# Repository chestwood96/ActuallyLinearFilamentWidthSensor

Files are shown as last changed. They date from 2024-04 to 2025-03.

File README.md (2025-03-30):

# ALFws (ActuallyLinearFilamentWidthSensor)
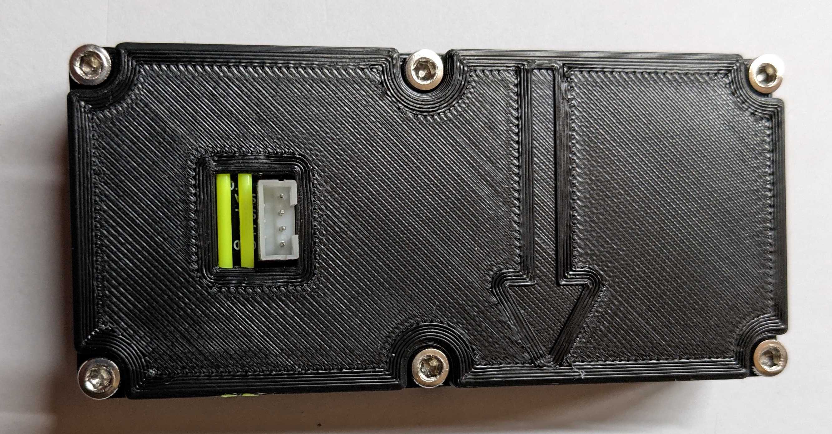
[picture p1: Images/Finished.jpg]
Finished sensor


## Features
### Sensor
- Very good linearity over 1mm (centred on ~1.75)
- Good linearity over 2-3mm (3mm filament is theoretically compatable, but remains untested)
- No thermal drift on the sensor
- Low drag
### Software
- Filament width compensation (of course)
- Logging filament diameter
- Undersize runout
- Oversize runout (so really oversized filament doesn't get stuck in the heatbreak)
- Delayed runout

## Why would you want that?
I mainly started this project ages ago because my local filament manufacturer doesn't know what QC is and happily ships filament with more than +/- 0.25mm tolerances. This isn't my first attempt at a filament width sensor but it is by far my best. With this I can print massively undersized or oversized or perfectly sized filament without ever having to touch my extrusion multiplier.

## BOM
### Electronics
- 1x [Sensor PCB](PCB/README.md)
- 1x JST PH 4pin female cable
### Mechanical
- 2x 6804 ball bearing
- 2x 6x3mm OR 1x 6x6mm magnet (if you can, get SmCO ones, they have less thermal drift)
- 2x 5x15 coil spring, 0.6mm wire diameter OR 8x 6x3mm neodymium magnets, the cheap kind
- 8x m3x8 screws
### Tools
- Fine-ish sanding pad/sandpaper
- Pliers
- Sidecutters
- Hammer or some other heavy object to hit stuff with
- 1.5mm and 2mm drill bit or other cylindrical metal objects of known size in that range for calibration

## Printing
Unless you want to constantly recalibrate this thing you need to print it in ABS or some other option that doesn't creep (definitely not PLA or Nylon), also avoid fiber filled filaments. The files are designed to print in the orientation they come in and do not require supports.

For MainBody **IRONING IS REQUIRED** since it is pretty much impossible to sand the inside sliding surface well enough, for the rest except the lid it is just highly recommended.

Except for MainBody the parts **need to be printed on a smooth buildplate**.

Use at least 3 perimeters and 5 top and bottom layers.

# Build
This is kind of a precision instrument and the quality of the final result heavily depends on how well it was assembled. Unfortunately this involves sanding.
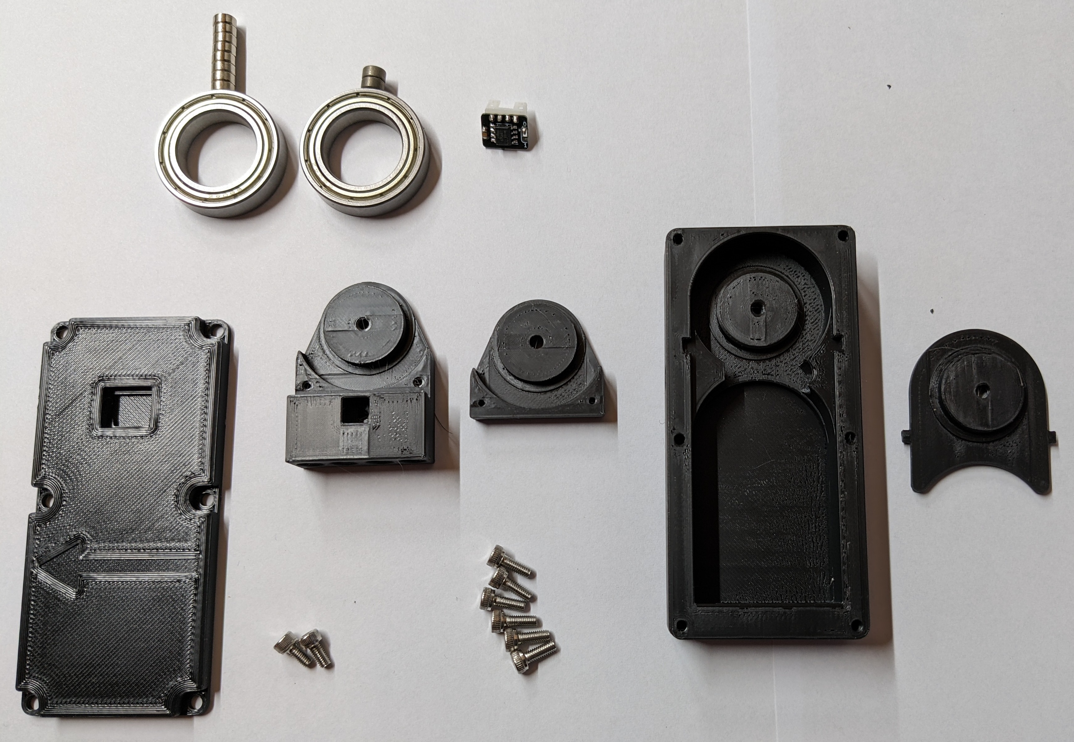
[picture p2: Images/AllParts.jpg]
All the parts layed out

Pretend the two m3x6 screws on this picture are also m3x8

## Cleaning up MainBody
Make sure the walls of the sliding surface on the bottom and the sides are smooth and have nothing sticking out. In most cases this should be fine off the printer but in this one there was a little defect in the walls. Also make sure the top surface for the lid is smooth and flat.
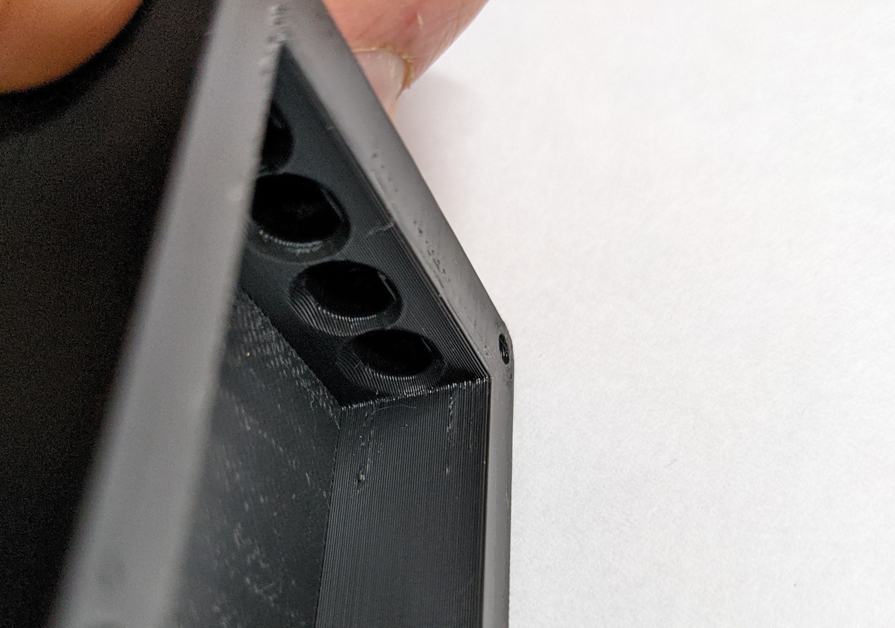
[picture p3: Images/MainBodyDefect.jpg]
Defect in MainBody

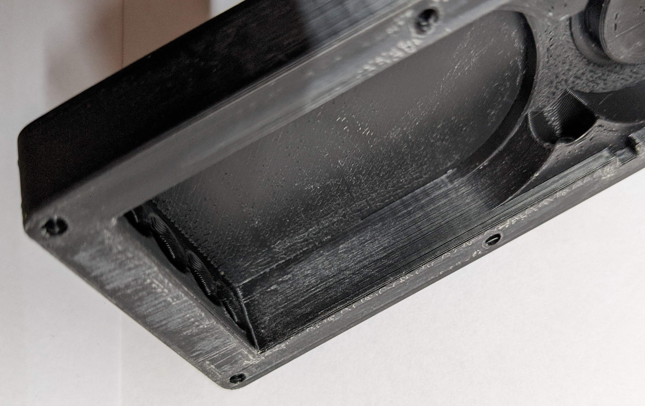
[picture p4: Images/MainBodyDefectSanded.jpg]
Defect in MainBody sanded

## Assembling the plunger
Place the bearing on MainPlunger and place BearingTop on top of that.
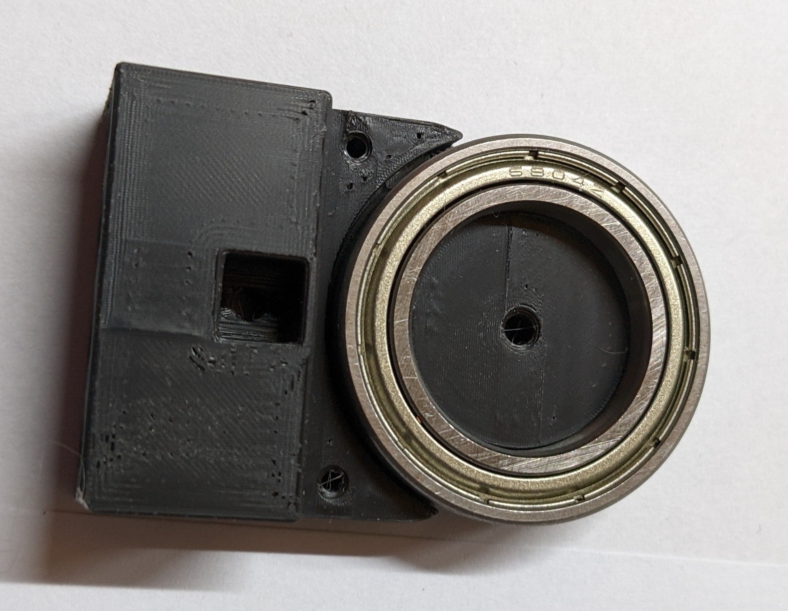
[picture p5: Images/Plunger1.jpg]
MainPlunger

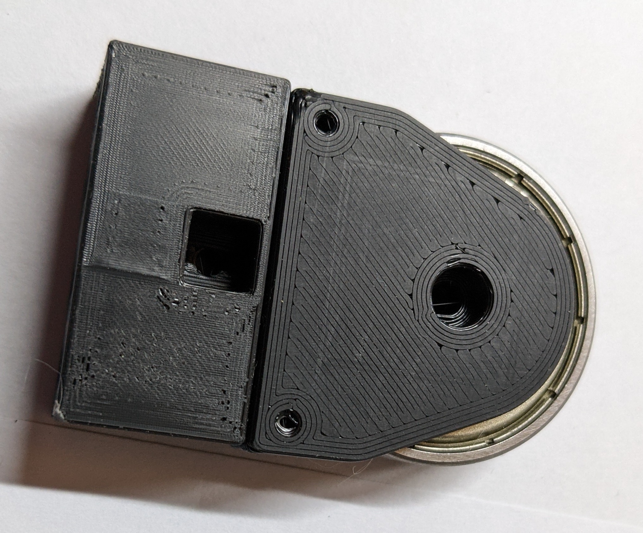
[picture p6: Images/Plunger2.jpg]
MainPlunger with BearingTop

Take a piece of the filament you printed with, sharpen the end, then push it through the pin hole. You may need to drill out the holes in BearingTop if the filament doesn't fit. Push them in most of the way, cut the filament a couple mm from the top, and hammer it in the rest of the way. Once it is all the way in snip it off as flush as you can.
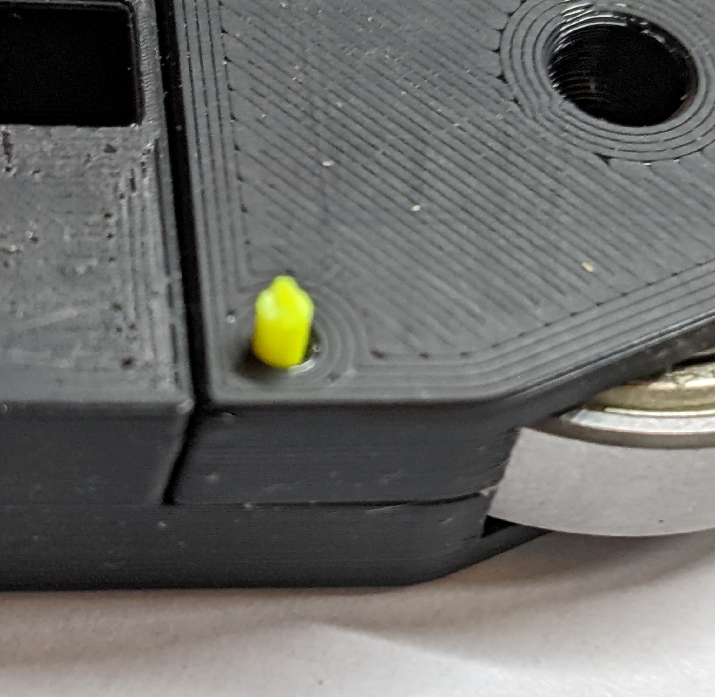
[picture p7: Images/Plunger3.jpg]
Plunger with pin in one side

Screw the bearing down using an m3x8 screw.
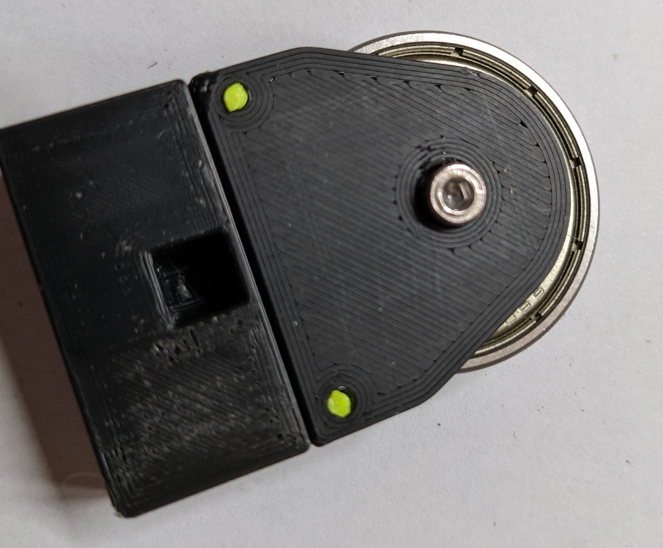
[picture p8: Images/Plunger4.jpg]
Plunger with pin in one side

Place your magnets (the nice ones if you got them) in the slot and gently (SmCO magnets are quite fragile and chip easily) press them all the way down, they should be a little bit below the surface of the part. They should be held in place pretty well. **If they don't sit in there snugly, glue them down using epoxy or something**, we don't wan't wobbly magnets.
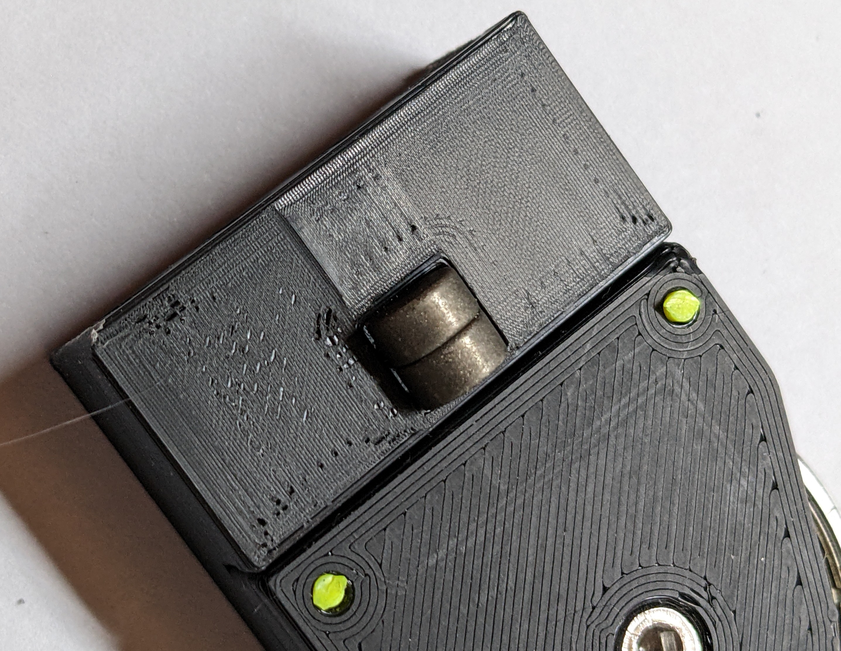
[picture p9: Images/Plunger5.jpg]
Magnet in slot

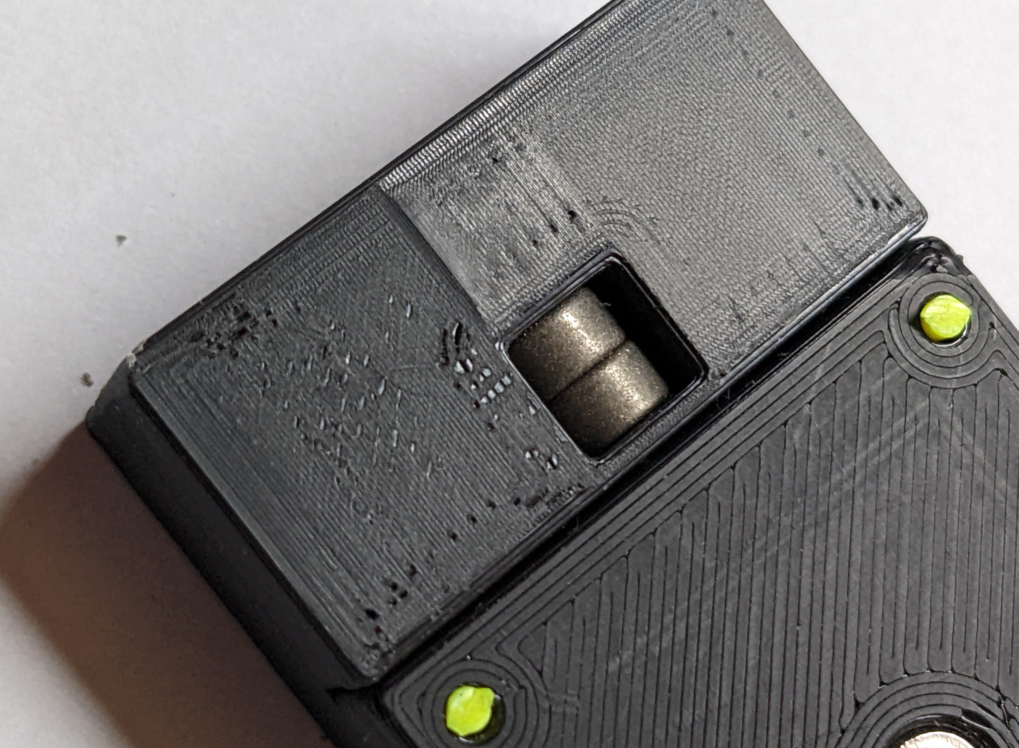
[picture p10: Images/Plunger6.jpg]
Magnet in slot all the way down


## Fitting the plunger
**Only sand with the sandpaper below the part** and avoid getting dust into the bearing, or it will seize and become crunchy. It is recommended to fix the sandpaper to a flat surface and move the part across the sandpaper. This avoids inadvertently making the part unlevel.

Sand the sides of the plunger until it slides smoothly. You don't want to sand too much otherwise you'll get side to side play.
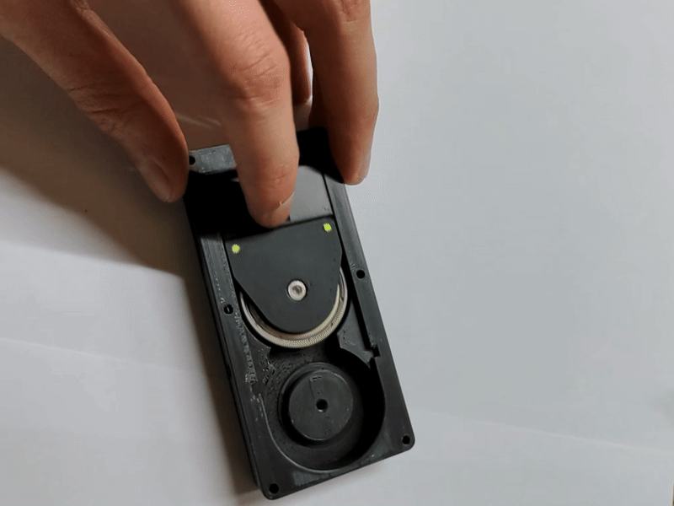
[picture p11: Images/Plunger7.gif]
Plunger sliding smoothly


*If you are using coil springs skip this step*

Push 2 magnets into each of the outer holes on the plunger, both facing in the same direction. The inner holes remain unused (could be used for more magnets if for some reason more spring force is required)
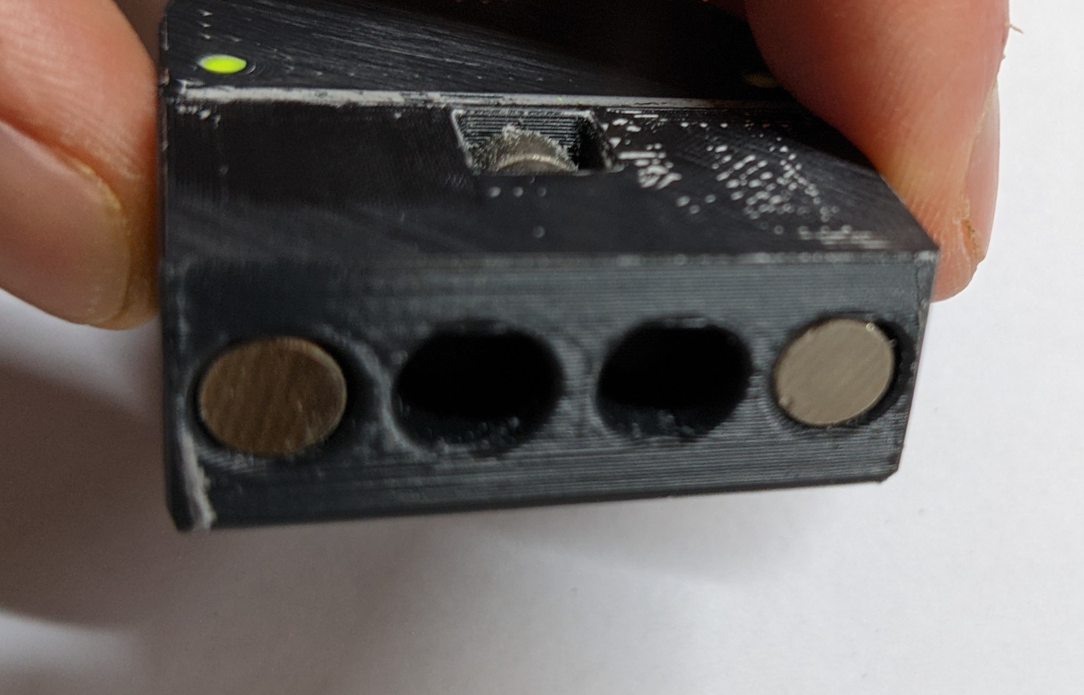
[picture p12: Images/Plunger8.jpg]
Magnets in plunger

Sand down the top of the plunger (the bottom should already be smooth) until you can freely shake it around with the lid closed. Start by just holding the lid closed by hand (only grip at the corners) and then when that works screw in the 2 middle screws and check again. You want to remove as little as possible so you get smooth motion and not a lot of play.
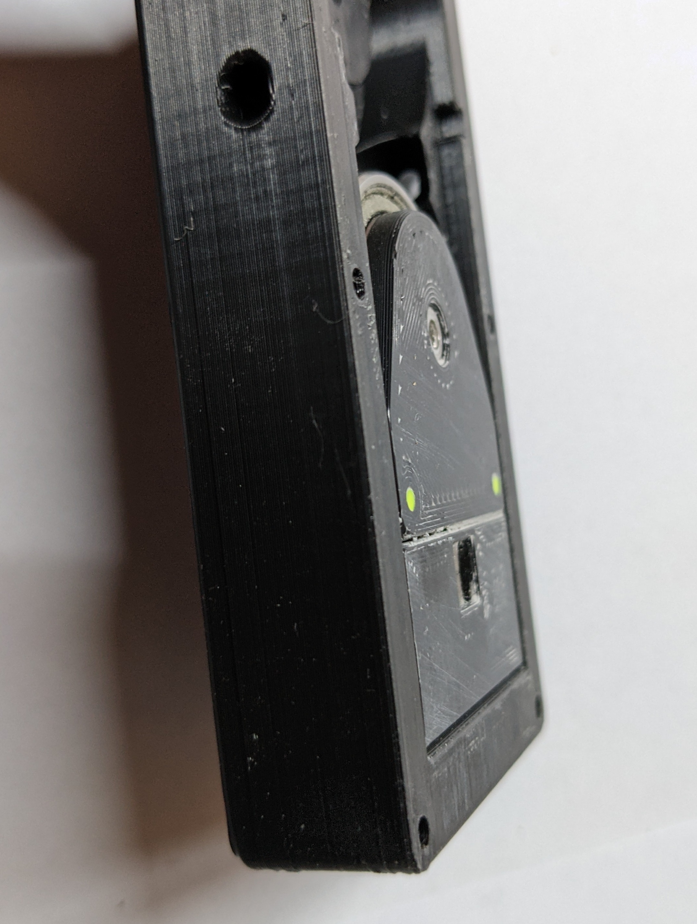
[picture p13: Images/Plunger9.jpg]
Sanded Plunger

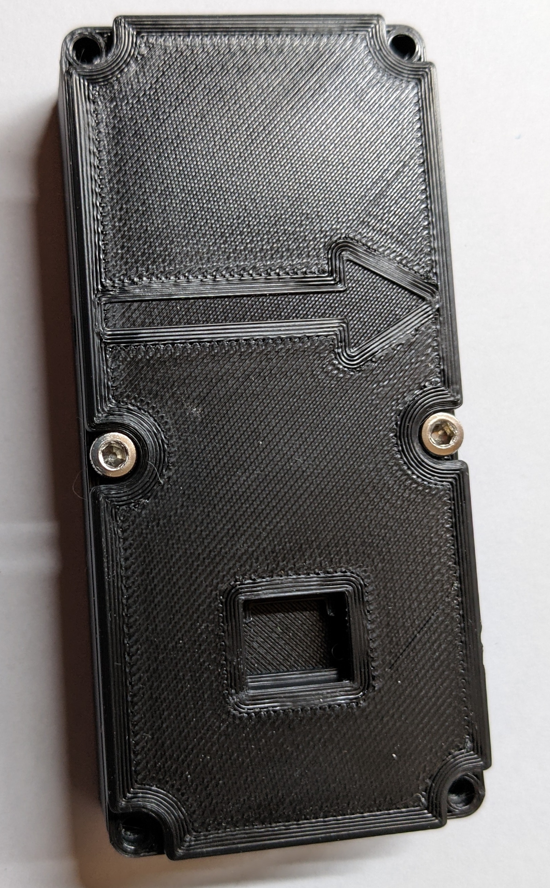
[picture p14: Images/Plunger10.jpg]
Sensor closed for testing


## Putting it all together
*If you are using coil springs skip this step*

Put the other 2 stacks of magnets into the holes as shown. The plunger should be attracted to the back of the sensor body like in the second picture. The magnets should now work as springs.
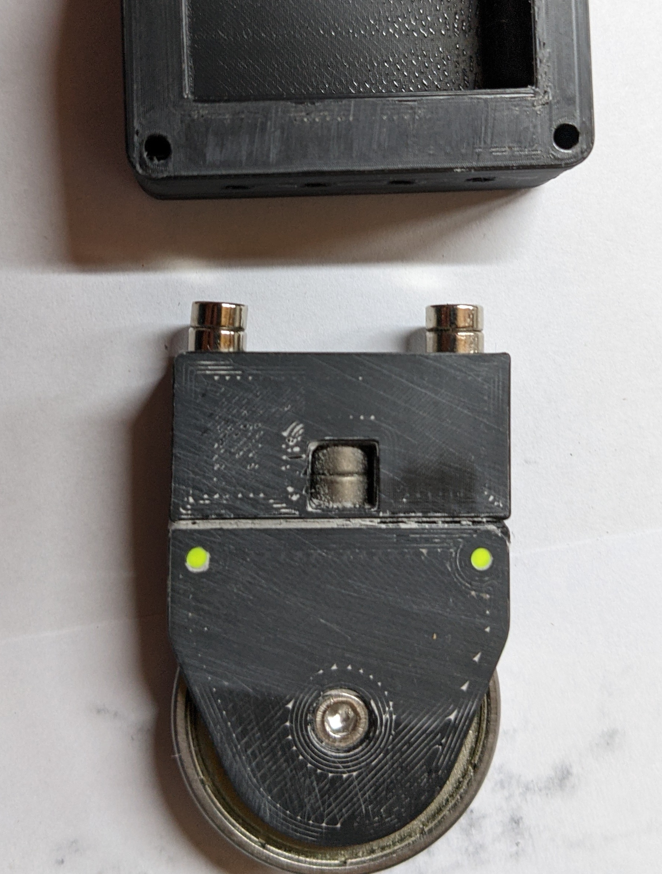
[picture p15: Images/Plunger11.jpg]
Magnets on the plunger

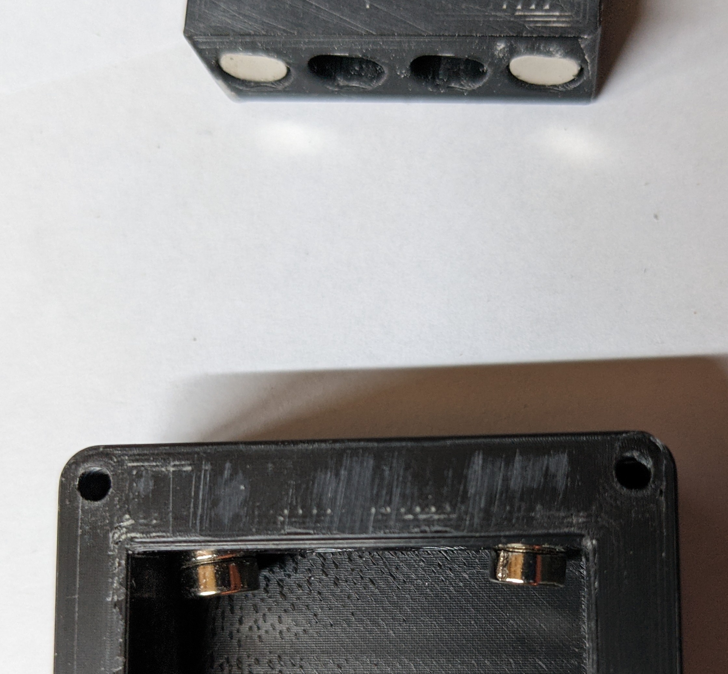
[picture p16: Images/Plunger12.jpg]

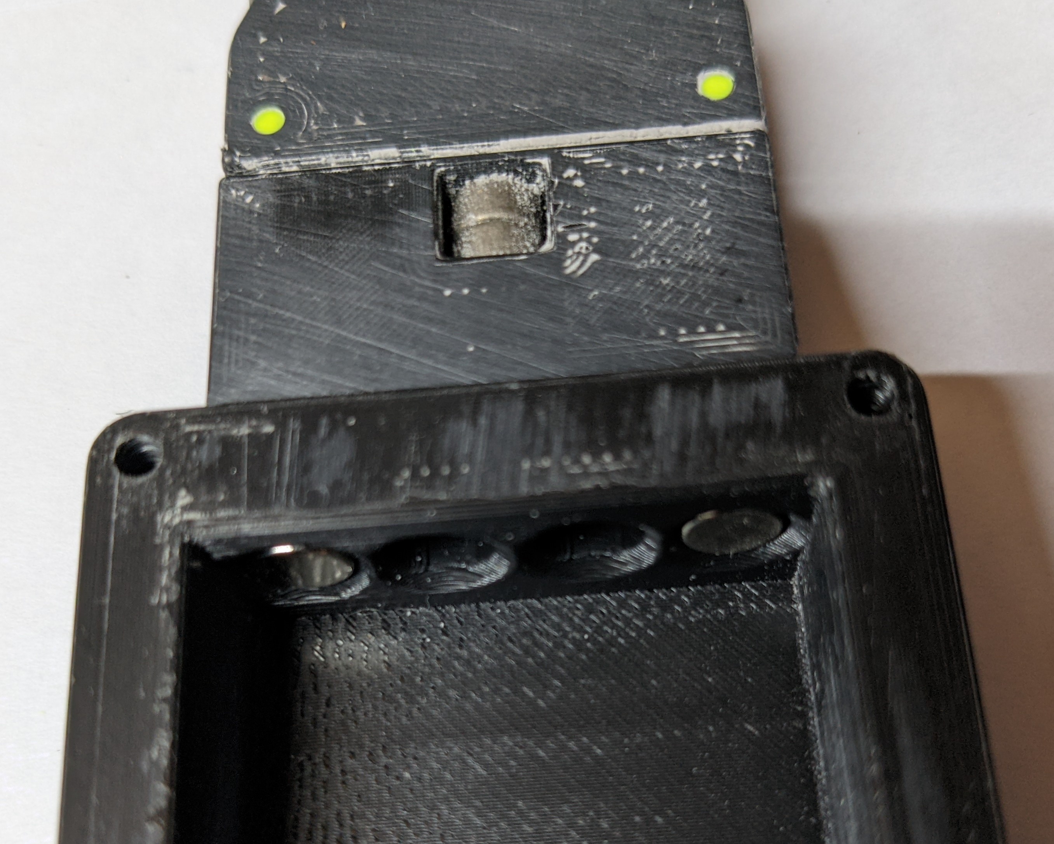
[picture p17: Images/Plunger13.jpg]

Demonstration of the magnet spring
Put the second bearing into MainBody, put BodyBearingHolder on top of it and screw it down. The bearing holder should not stick out the top, if it does sand it down.
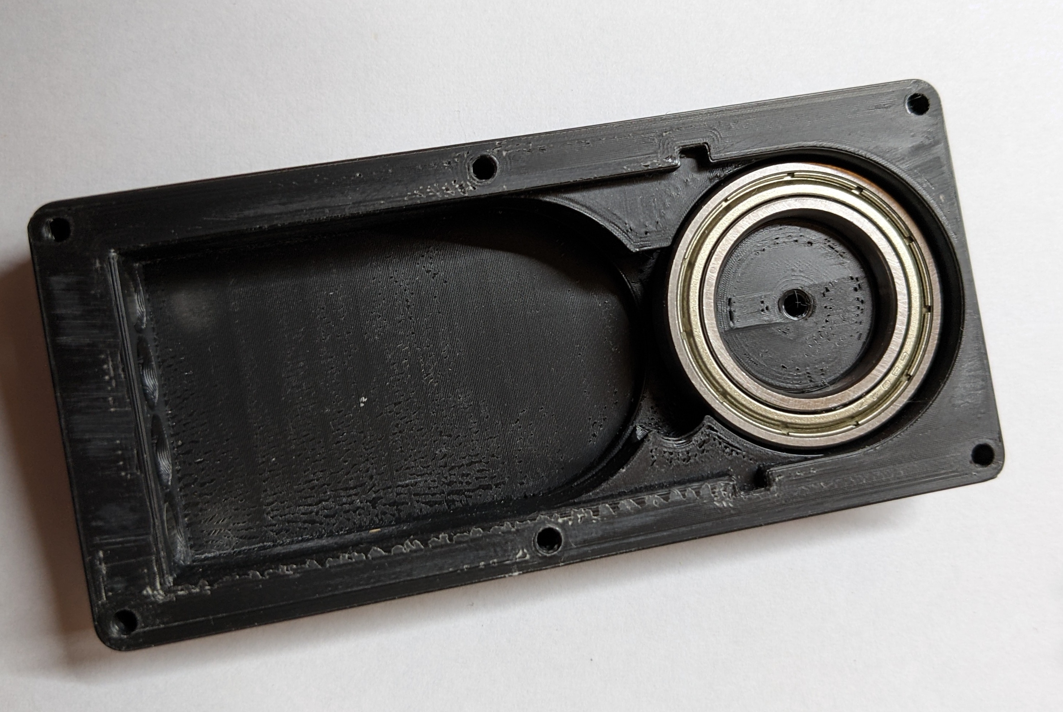
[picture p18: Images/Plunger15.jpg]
Bearing in body

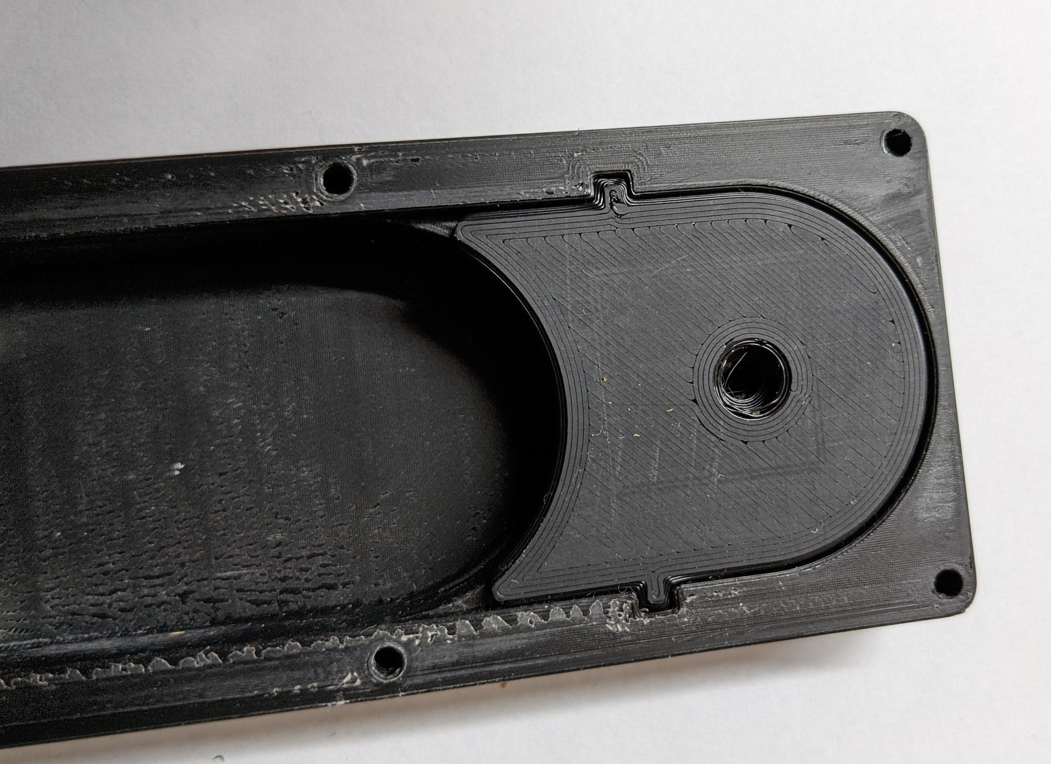
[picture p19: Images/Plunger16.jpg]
Bearing holder in body

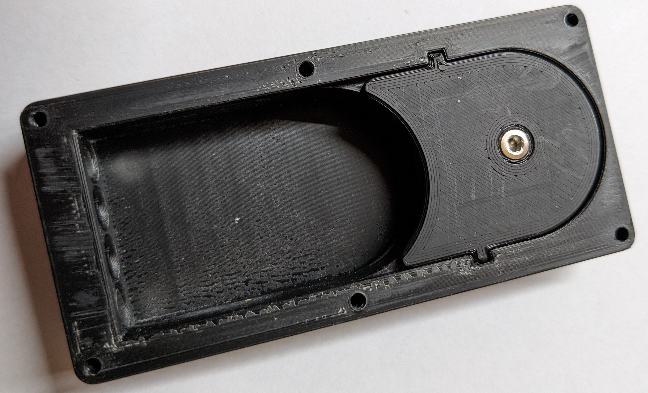
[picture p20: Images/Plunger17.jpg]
Bearing holder screwed down


*If you are using coil springs put the springs into the outer holes when putting in the plunger*

Place the plunger into the body. It's normal that the bearings don't completely touch when closed but they should get within less than 1mm.
Bearing holder screwed down

## Putting the sensor in the lid
**While the sensor is still free, note what jumper value is set because you won't be able to see it later, and if none is set fix that**

Gently push the sensor board into the hole in the lid as shown.
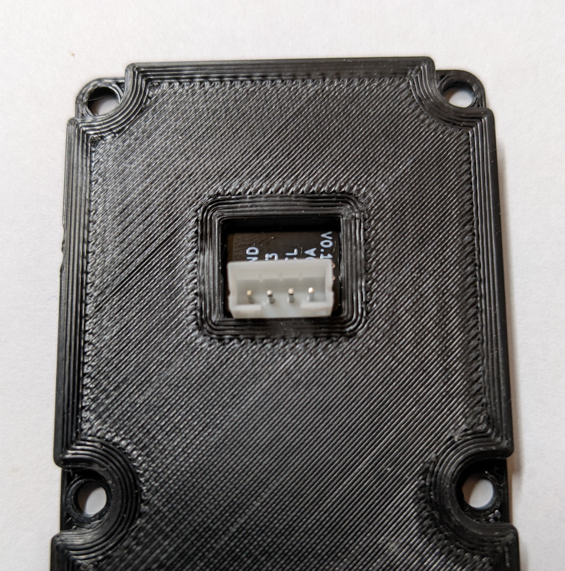
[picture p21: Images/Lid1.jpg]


Push a sharpened piece of ABS filament into the hole on the side of the lid, over the sensor and into the hole on the other side. Once you reach the entrance of the inner hole, cut the filament about 2mm from the side and hammer it the rest of the way in, it should be flush otherwise cut the rest off. Then repeat for the second hole.

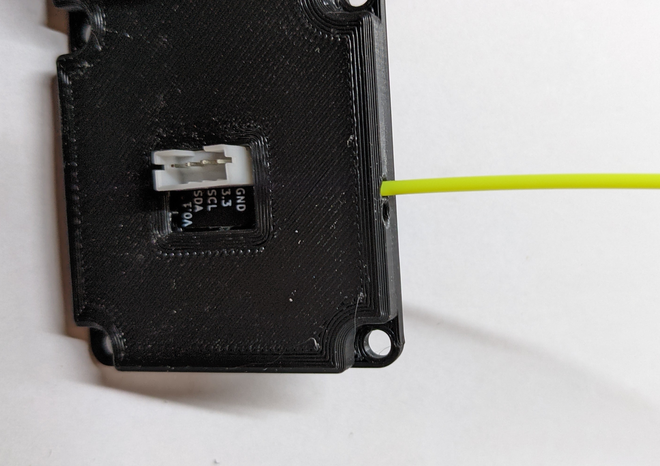
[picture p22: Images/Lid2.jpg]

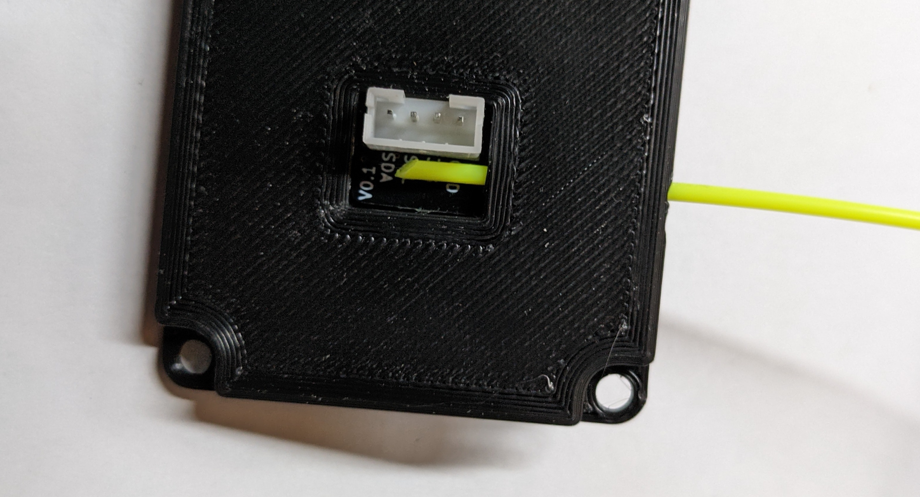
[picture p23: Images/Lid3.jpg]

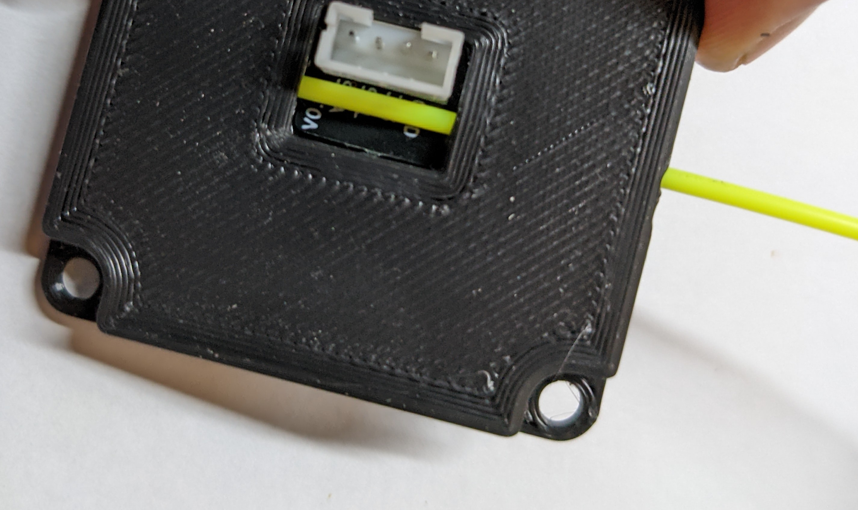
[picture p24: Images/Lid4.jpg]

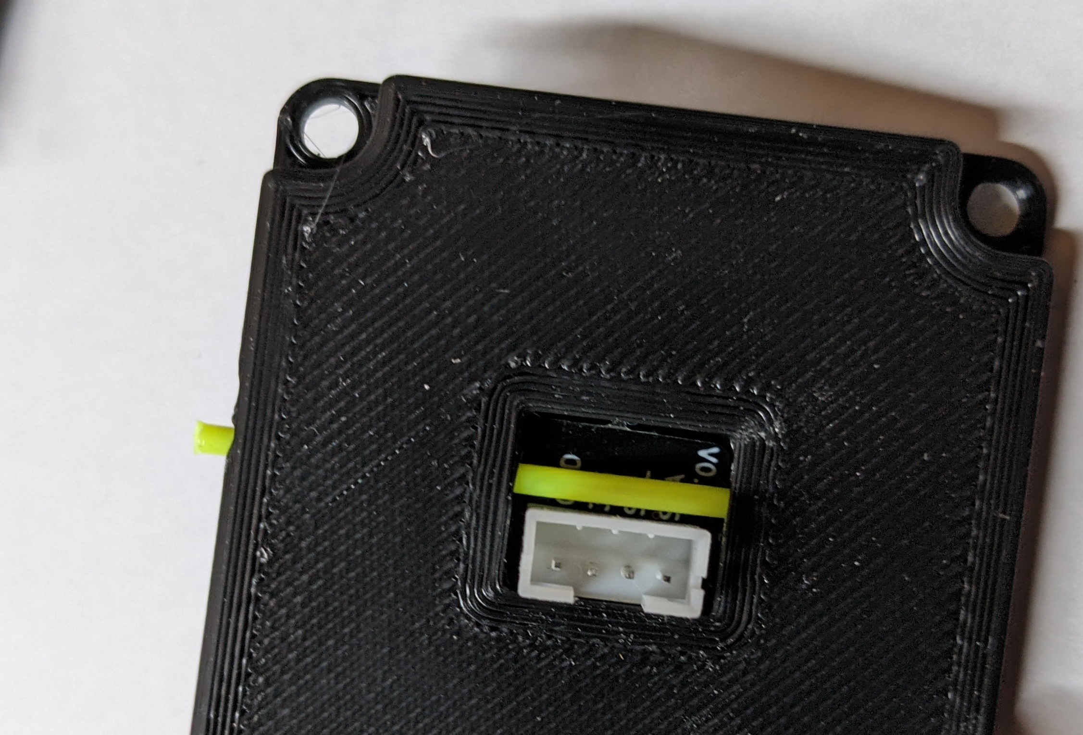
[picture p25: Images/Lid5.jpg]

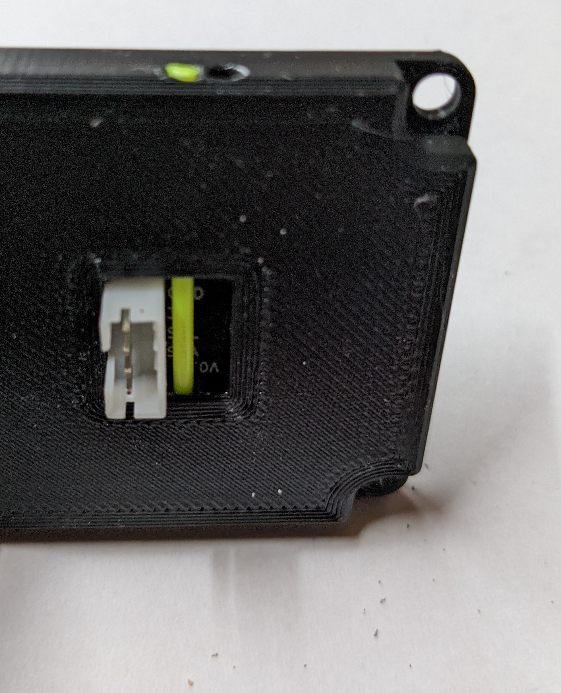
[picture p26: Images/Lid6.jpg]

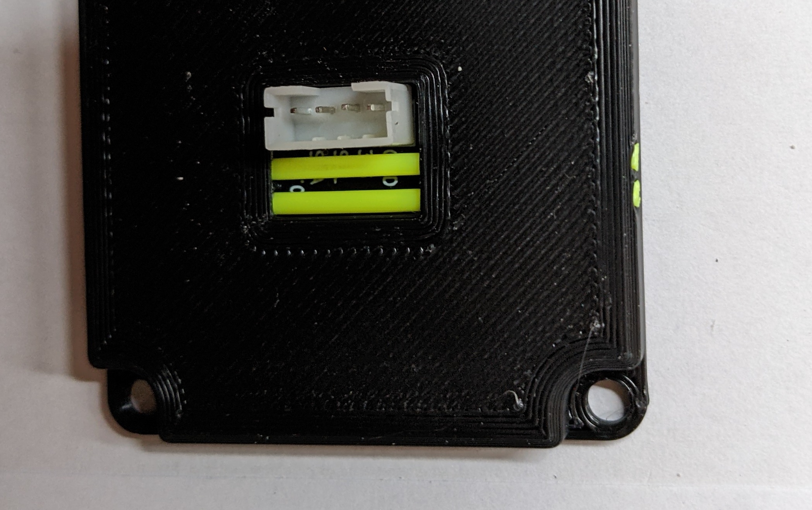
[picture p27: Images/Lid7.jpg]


## Putting on the lid
Make sure the sensor part is over the magnet in the plunger and close the lid using 6 m3x8 screws.
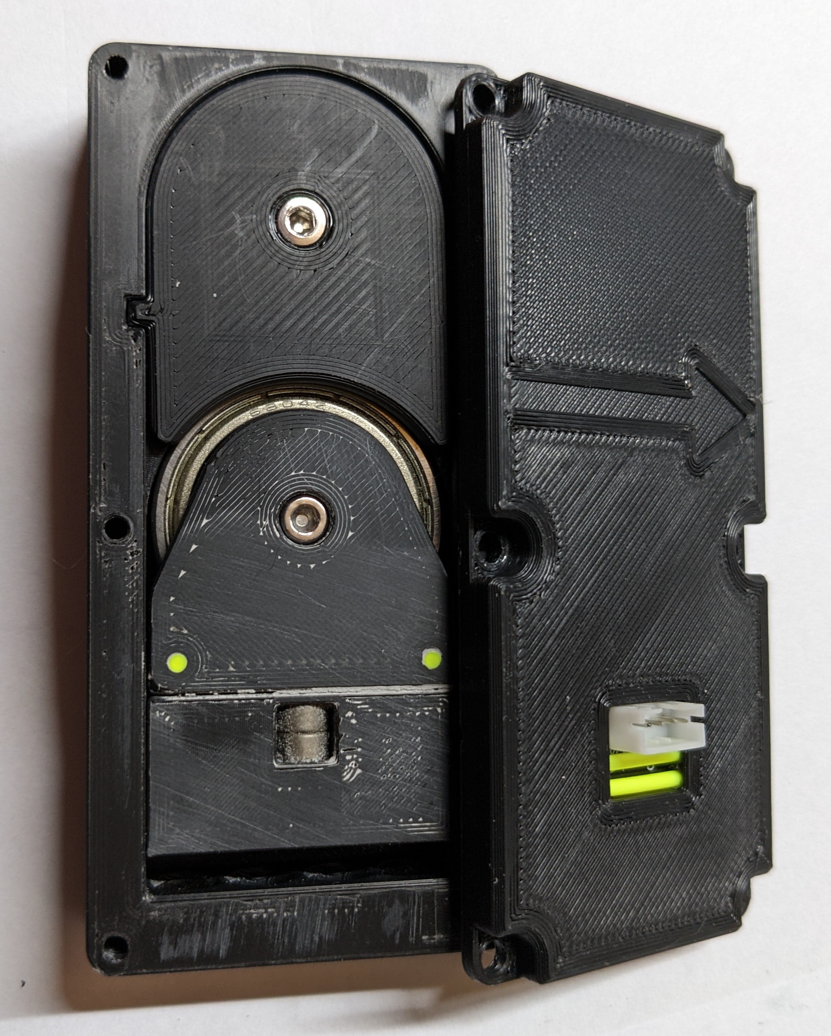
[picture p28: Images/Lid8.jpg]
Lid orientation

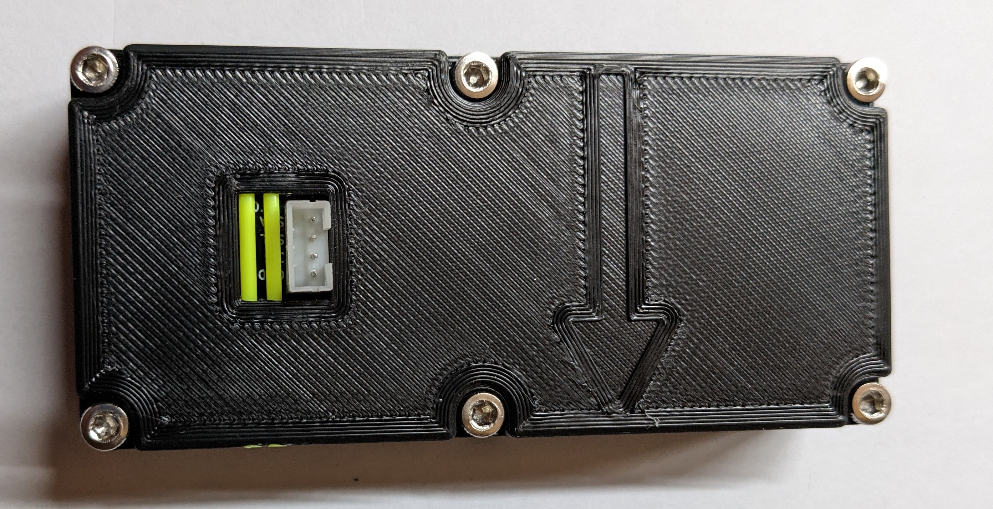
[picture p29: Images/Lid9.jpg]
Done


**Congratulation the sensor is built** 

Stick some filament in it, check if the bearings are running smoothy and the plunger closes up correctly once you pull it back out.

# Installation

## Wiring
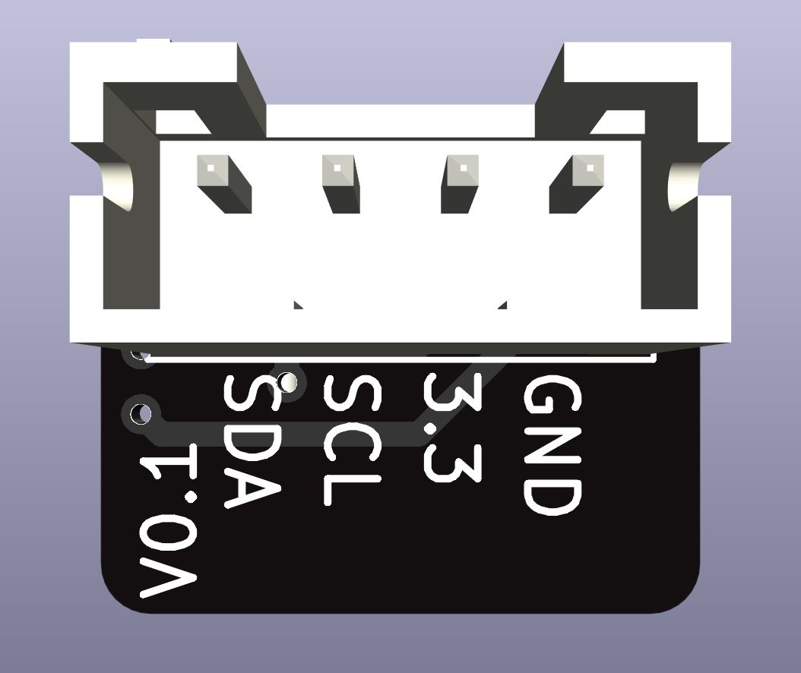
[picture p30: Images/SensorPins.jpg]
Sensor pins

**If you are somehow still on a platform with 5V IO pins you are going to need a level shifter for SDA and SCL. Examples include ATMEL based boards like ramps and the old creality boards. If in doubt measure the voltage on the SDA pin before connecting.**

Find an available I2C port on yur mainboard and connect the sensor to it. While you can theoretically use any pins with software I2C, I recommend using HW I2C since the sensor produces quite a bit of I2C traffic which would take up quite a lot of the MCUs computing power.

For example I use the I2C port on PB8 and PB9 on the octopus pro.
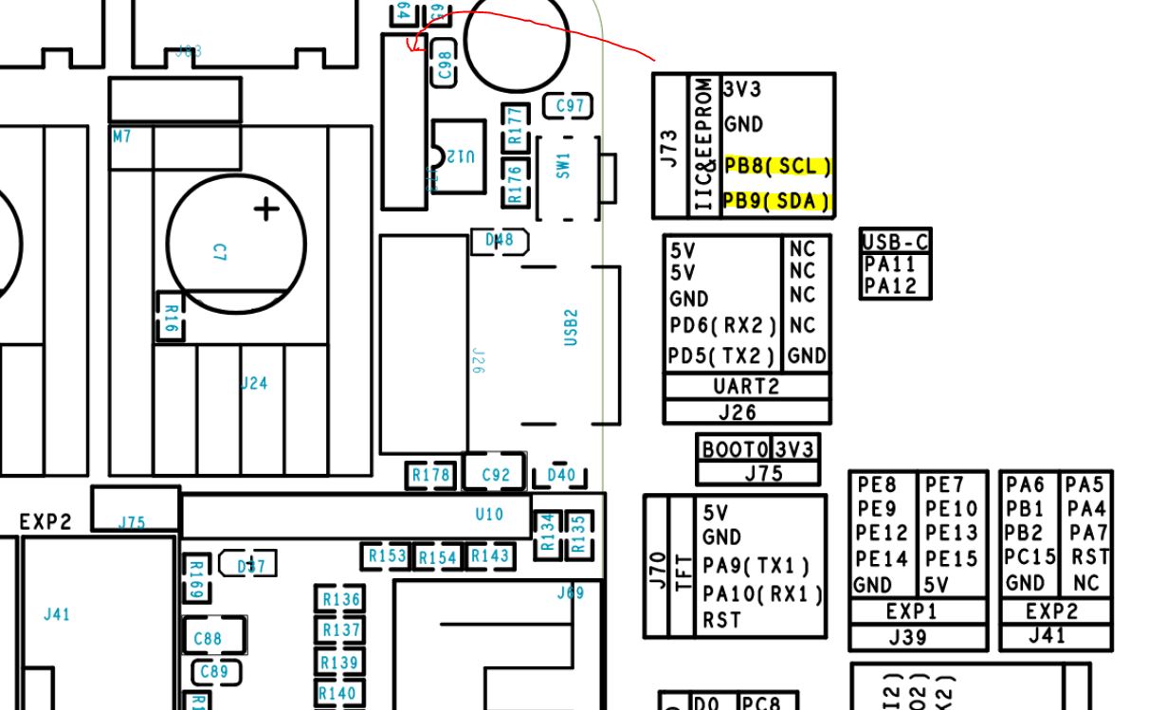
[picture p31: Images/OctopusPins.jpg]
Octopus pro i2c


Alternatively you could use a separate microcontroller like a Pi Pico, STM32 bluepill or anything else supported by Klipper.

Simply connect the pins on the sensor to the corresponding ones on your board (GND to GND, 3.3V to 3.3V, SDA to SDA and SCL to SCL).

Make sure the wire is as short as necessary, the longer it is the more interference it will have and klipper will shut down from a single failed I2C transmission, as non-essential it may be (would be cool if someone fixed that at some point but it is what it is for now).

## Mounting
While I do leave mounting as a bit of an exercise for the user I do supply a known working "reference design".

Ultimately you just need to put the sensor in the filament path but the exact mounting method makes quite a difference on the data it generates. For best results the filament path should be constrained for about 10-30cm before and after the sensor, as well as pushed slightly towards the fixed bearing on the sensor. Failing to constrain the filament path should not hinder operation, but it will add a ton of noise to the data. Confining the filament path is recommended for this reason. 

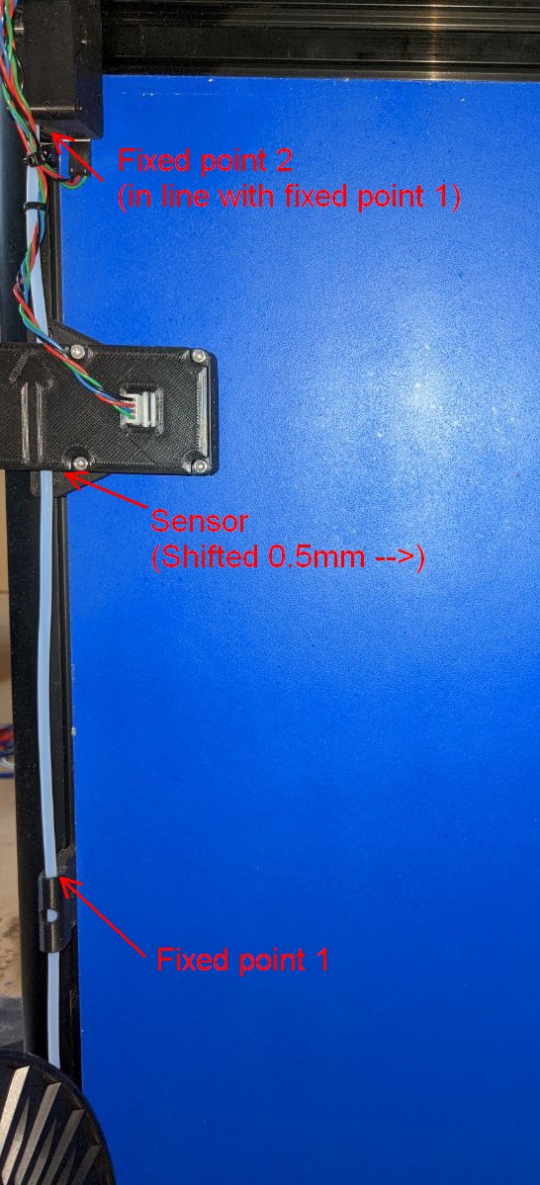
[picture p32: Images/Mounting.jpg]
Mount example


I have included STLs for a 0.5mm offset mount for the sensor and tube holders that fit into 6mm wide 2020 channels as a starting point. If you design a nice mount for yourself feel free to submit it as a pull request.

# Software

## Disclaimer
This version of the code requires Klipper commit [`272e815`](https://github.com/Klipper3d/klipper/commit/272e815522b0bc8e0806e052b73a5cc1af979cd7) or newer.  
Using an older Klipper version may cause compatibility issues.

## Installing the software
Copy **filament_width_sensor_hall_mlx90395.py** and **filament_width_compensation.py** from the "Software" folder into your klipper install under "klippy/extras/" and restart the klipper service.

## Klipper configuration
Add the following section to your klipper config:

```
[filament_width_sensor_hall_mlx90395 mlx1]
#i2c_mcu: sensorBoard
i2c_bus: i2c1a
i2c_speed: 400000
i2c_address: 12 # 12 if addr 0, 13 if add 1
cal_dia1: 1.5
cal_dia2: 2.0
raw_dia1: 32000
raw_dia2: -32000

[filament_width_compensation]
sensor: mlx1
compensation_enabled: false
runout_enabled: true
oversize_enabled: true
logging: true
default_nominal_filament_diameter: 1.75
poll_time: 0.1
measurement_interval: 1
measurement_delay: 1000
runout_delay: 0
use_current_dia_while_delay: false
max_difference:0.2
runout_diameter: 1.4
oversize_diameter: 1.9
pause_on_runout: true
```

Replace ```i2c_bus``` with the one you are actually using. You can look up the names on mainsail by going to "Machine" then clicking the name of the MCU. My case turned out to be I2C1a. If your sensor isn't on the main mcu you'll also need to set ```i2c_mcu``` accordingly.

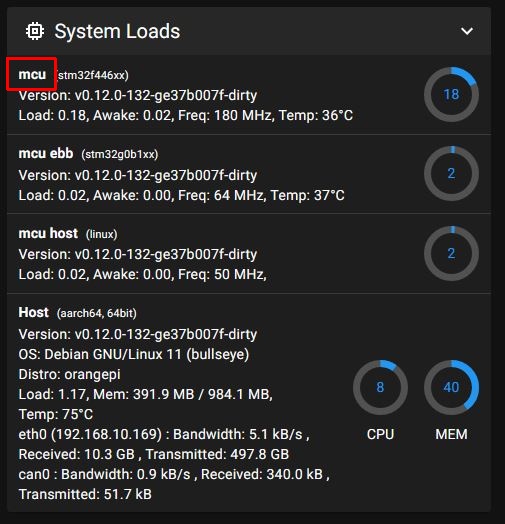
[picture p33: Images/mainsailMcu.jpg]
mcu

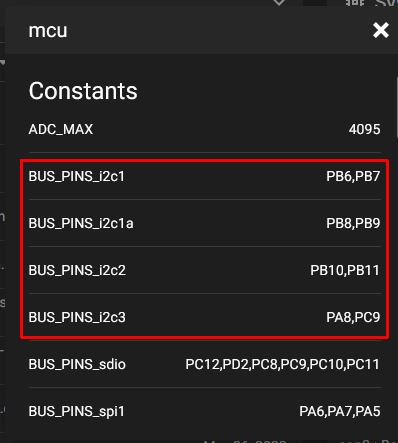
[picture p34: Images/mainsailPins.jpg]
bus names


Depending on which jumper you bridged select your ```i2c_address``` (0=12, 1=13).

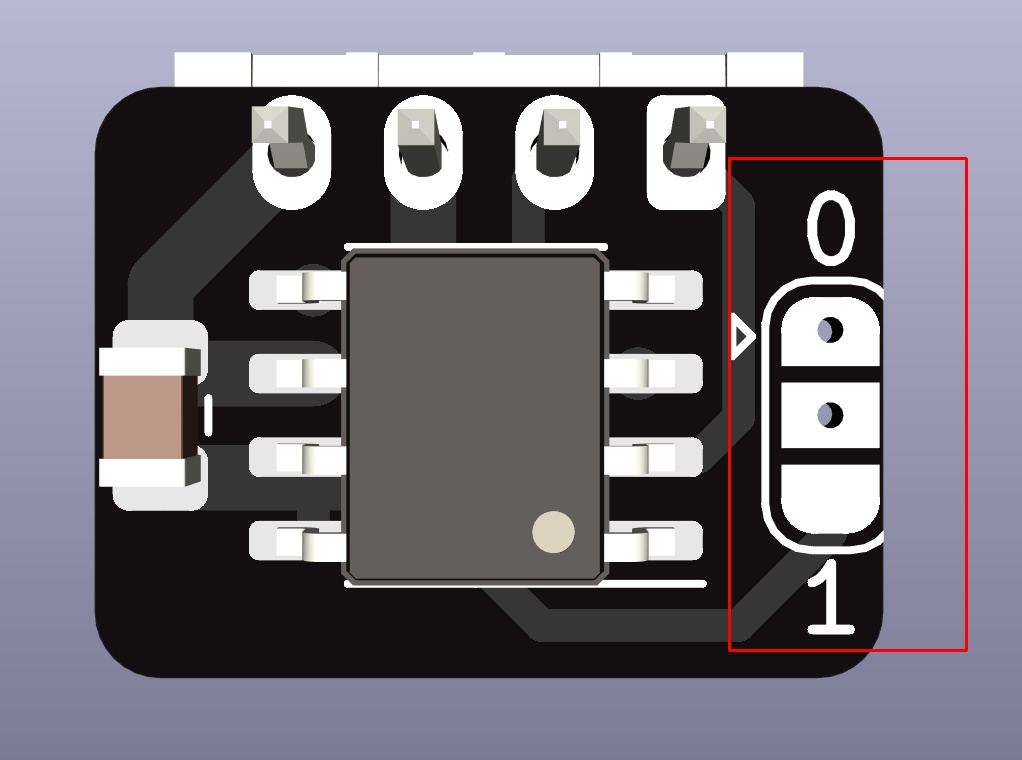
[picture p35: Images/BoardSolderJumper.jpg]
Solder jumper location


Set ```measurement_delay``` to the distance between the center of the sensor and about the middle of the meltzone in mm.

At this point you can restart klipper and if everything went well it should start up fine.

If you are curious you should now find the unique ID of your sensor in the logs by searching for "MLX90395 with ID:". Not sure what to do with that information but if that log line is there it definitely connected.

Check if you can read the sensor using '''MLX_QUERY_RAW SENSOR=mlx1''', this should give you a raw reading of the sensor.

## Calibration
For calibration you'll need 2 reference pieces around the target size, I used 1.5mm and 2mm drill bits.

First measure your reference pieces, in my case the 1.5mm drill bit measures at 1.485mm and the 2mm one at 1.995mm. Enter those values as ```cal_dia1``` and ```cal_dia2``` in your sensor config (no need to restart yet).

Now gently put your first reference piece into the sensor, making sure it is nicely between the bearings and not getting caught somewhere else. Wiggle it around and push and pull a bit, then take a reading using ```MLX_QUERY_RAW SENSOR=mlx1 AVERAGING=100```, I got 30 for the 1.5mm sample. Note your value as ```raw_dia1```. Then repeat the whole thing for your second sample (in this case I got -15612) and note that in ```raw_dia2```.

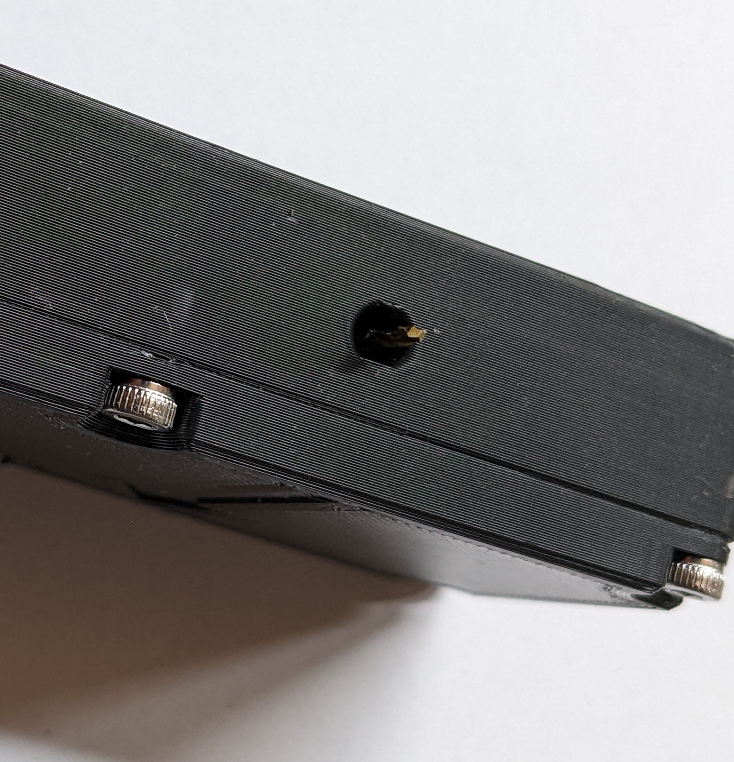
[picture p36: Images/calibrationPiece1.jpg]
1.5mm calibration piece in the sensor


Putting that all together my calibrated sensor now looks like this (just as an example, no value in copying any of that)
```
[filament_width_sensor_hall_mlx90395 mlx1]
i2c_bus: i2c1a
i2c_speed: 400000
i2c_address: 12 # 12 if addr 0, 13 if add 1
cal_dia1: 1.485
cal_dia2: 1.995
raw_dia1: 30
raw_dia2: -15612
```

## Verifying calibration
Check if your calibration worked by putting your reference sample back in and calling ```QUERY_FILAMENT_WIDTH```, if it worked you should get the diameter of your reference piece, repeat with the other one and some filament.

Make sure the sensor reads less than ```runout_diameter``` when empty. Adjust ```runout_diameter``` if necessary (though if the default value is too low, there may be assembly or calibration errors).

Set ```oversize_diameter``` to something below the thinnest diameter in your filament path. For dragon I would not go above 1.9mm, other hotends my be able to take more.

# Using filament width compensation
So far you have a really fancy filament runout sensor that knows the diameter of the filament. Next comes the interesting part, actually using filament width compensation.

You can activate it by setting ```compensation_enabled``` to true or temporarily enable or disable compensation using the ```ENABLE_FILAMENT_WIDTH_COMPENSATION``` and ```DISABLE_FILAMENT_WIDTH_COMPENSATION``` commands.

With filament width compensation you need to recalibrate your extrusion multiplier for your filaments. Keep in mind you must extrude at least ```measurement_delay``` before calibration actually kicks in, so don't try calibrating before that.

After that you should not have to worry about the actual diameter of your filament anymore.

**Important: always clear the filament array after loading filament**

You can clear the array using the ```CLEAR_FILAMENT_ARRAY```. If you don't do that it'll compensate on wrong data and may actually make things worse.

If you have a filament loading macro it may make sense to add it to that.

# Config options
## [filament_width_sensor_hall_mlx90395]
```
[filament_width_sensor_hall_mlx90395 my_sensor]
#i2c_mcu:
#   The name of the micro-controller that the chip is connected to.
#   The default is "mcu".
#i2c_bus:
#   If the micro-controller supports multiple I2C busses then one may
#   specify the micro-controller bus name here. The default depends on
#   the type of micro-controller.
#i2c_speed:
#   The I2C speed (in Hz) to use when communicating with the device.
#   The Klipper implementation on most micro-controllers is hard-coded
#   to 100000 and changing this value has no effect. The default is
#   100000. Linux, RP2040 and ATmega support 400000.
#i2c_address:
#   The i2c address of the device. This must specified as a decimal
#   number (not in hex). The default is 12.#
#   12 if addr 0, 13 if add 1
#cal_dia1:
#cal_dia2:
#   The calibration values (in mm) for the sensors. The default is
#   1.50 for cal_dia1 and 2.00 for cal_dia2.
#raw_dia1:
#raw_dia2:
#   The raw calibration values for the sensors. The default is 10000
#   for raw_dia1 and -10000 for raw_dia2.
```
## [filament_width_compensation]
```
[filament_width_compensation]
sensor:
#   Name of the filament width sensor
#compensation_enabled:
#   Compensation enabled or disabled after power on. The default is to
#   disable.
#runout_enabled:
#   Runout enabled or disabled after power on. The default is to
#   disable.
#oversize_enabled:
#   Oversize runout enabled or disabled after power on. The default is to
#   disable.
#logging:
#   Filament width logging enabled or disabled after power on. The default is to
#   disable.
#default_nominal_filament_diameter:
#   The nominal filament diameter (what the "correct filament width is assumed to be").
#   needs to be provided and >1
#poll_time: 0.1
#   How long to wait between taking readings in seconds default is 1
#measurement_interval: 1
#   The minimum distance between readings in the compensation buffer
#measurement_delay: 1000
#   The distance from sensor to the meltzone in
#   millimeters (mm). The FIFO buffer keeps each sensor value and
#   position in an array and POP them back in correct position. This
#   parameter must be provided.
#runout_delay: 0
#   How much before the meltzone (based on measurement delay) it should stop on runout in mm. 
#   For example 200 would mean stop 200mm in front of the meltzone, keep in mind after the runout
#   is triggered it doesn't stop instantly so leave enough extra.
#   The default is 0 (disable delayed runout entirely and stop right at the sensor)
#use_current_dia_while_delay:
#   If the compensation should use the first reading it got while the buffer catches up (after power up
#   or buffer clear). Otherwise it will use default_nominal_filament_diameter.
#   The default is false
#max_difference:
#   Maximum allowed filament diameter difference in millimeters (mm).
#   If difference between nominal filament diameter and sensor output
#   is more than +- max_difference, extrusion multiplier is set back
#   to %100. The default is 0.200.
#runout_diameter:
#   Diameter below which a runout is triggered (if runout is enabled)
#   The default is 1.0
#oversize_diameter: 1.9
#   Diameter above which a runout is triggered (if oversize is enabled)
#   The default is 1.9
#pause_on_runout: True
#   When set to True, a PAUSE will execute immediately after a runout
#   is detected. Note that if pause_on_runout is False and the
#   runout_gcode is omitted then runout detection is disabled. Default
#   is True.
#runout_gcode:
#   A list of G-Code commands to execute after a filament runout is
#   detected. See docs/Command_Templates.md for G-Code format. If
#   pause_on_runout is set to True this G-Code will run after the
#   PAUSE is complete. The default is not to run any G-Code commands.
#insert_gcode:
#   A list of G-Code commands to execute after a filament insert is
#   detected. See docs/Command_Templates.md for G-Code format. The
#   default is not to run any G-Code commands, which disables insert
#   detection.
```
# Commands
## [filament_width_sensor_hall_mlx90395]
### MLX_QUERY_RAW
```MLX_QUERY_RAW SENSOR=<sensor> AVERAGING=<count>``` Allows requesting a raw reading from the specified sensor with optional averaging.

## [filament_width_compensation]
### QUERY_FILAMENT_WIDTH
```QUERY_FILAMENT_WIDTH``` requests a reading for the current sensor and displays it.
### DUMP_FILAMENT_ARRAY
```DUMP_FILAMENT_ARRAY``` dumps the current content of the filament width buffer to the console
### CLEAR_FILAMENT_ARRAY
```CLEAR_FILAMENT_ARRAY``` clears the filament width buffer
### ENABLE_FILAMENT_WIDTH_COMPENSATION
```ENABLE_FILAMENT_WIDTH_COMPENSATION``` Temporarily enables filament width compensation
### DISABLE_FILAMENT_WIDTH_COMPENSATION
```DISABLE_FILAMENT_WIDTH_COMPENSATION``` Temporarily disables filament width compensation
### ENABLE_FILAMENT_WIDTH_RUNOUT
```ENABLE_FILAMENT_WIDTH_RUNOUT``` Temporarily enables filament width runout
### DISABLE_FILAMENT_WIDTH_RUNOUT
```DISABLE_FILAMENT_WIDTH_RUNOUT``` Temporarily disables filament width runout
### ENABLE_FILAMENT_WIDTH_OVERSIZE
```ENABLE_FILAMENT_WIDTH_OVERSIZE``` Temporarily enables filament oversize runout
### DISABLE_FILAMENT_WIDTH_OVERSIZE
```DISABLE_FILAMENT_WIDTH_OVERSIZE``` Temporarily disables filament oversize runout
### ENABLE_FILAMENT_WIDTH_LOGGING
```ENABLE_FILAMENT_WIDTH_LOGGING``` Temporarily enables filament width logging
### DISABLE_FILAMENT_WIDTH_LOGGING
```DISABLE_FILAMENT_WIDTH_LOGGING``` Temporarily disables filament width logging
### SET_FILAMENT_WIDTH_OVERSIZE_DIAMETER
```SET_FILAMENT_WIDTH_OVERSIZE_DIAMETER OVERSIZE_DIAMETER=<dia>``` Temporarily sets the oversize diameter
### SET_FILAMENT_WIDTH_RUNOUT_DIAMETER
```SET_FILAMENT_WIDTH_RUNOUT_DIAMETER RUNOUT_DIAMETER=<dia>``` Temporarily sets the runout diameter

# FAQ (Or more like anticipated questions + a little man yelling at cloud )
## Why use such big bearings?
Turns out accurately measuring linear displacement is the easy part of this hole thing (and that already was quite a journey). Turning filament width into linear displacement accurately is where it gets really complicated. The sensor started off a lot smaller, the early development version were using 4mm pins. that worked well on the test machine and it was very useful for figuring out the magnet and sensor arrangement and testing thermal drift and stuff but once actual filament got into play it got a bit more complicated. 

Filament has a natural bend to it and there is tension on it, it can bow away from the fixed side and appear too large. This can of course be mitigated by using more force but then you start to squish the filament and squish introduces a whole other non linear source of error. Also with the 4mm pins the spring force required to pass the 180 test (a piece of filament reading the same with the bend towards the fixed bit and away from it) caused extreme drag and also squished the hell out of the filament. Then came small bearings to mitigate the drag, that worked but we still had a ton of squish so the bearings got bigger and bigger (the 6909 one was initially because I ordered the wrong bearings but was my daily driver for quite a while). I did consider adding squish compensation so I could go back to a more reasonable size but that would have added another ting to calibrate per material and I didn't really want to do that. After the discovery that confining the filament path helps a lot I was able to reduce the spring force a lot which also allowed me to go back to more reasonably sized bearings. With the current version there should be negligible squish.
## Why are there 4 spots for springs and we only use 2?
Leaves open the option to use more force, should not be necessary but the option doesn't hurt anyone.
## Why use such an obscure sensor instead of the abundant cheap analog ones the other sensors use?
When I was dealing with thermal drift, the first idea was ovenized sensors which worked but it's high complexity and would have made for a way more complicated build and configuration guide (I even had a sensor with an ovenized magnet to test the drift on those). Then I found that there are thermal compensated hall sensors and that there is a digital one for pretty much the same price as the analog ones. I tested both he analog ones and the digital one and like the digital one better. Their configurability made testing easier and it has a better adc than all the 3d printer mcus I know of that is also closer to the sensor.
## Does actually linear imply other sensors aren't?
At least all of the ones I know of. If that is actually a problem in practice I am not sure, deuterius reports good results with a sensor I know isn't linear but ultimately we are using cnc glue guns and even the non linear ones tend to read higher for higher and lower for lower just well not linearly so. But I want this sensor to remove variables not add new ones so I may have gone a bit overboard.
## Doesn't using 2 analog sensors in opposite direction cancel out thermal drift?
This sounds so good in theory and is one of the bigger contributors to me going down this rabbithole. Instead of just going with it my dumb ass just had to test it. Theoretically if both sensors had the exact same thermal drift (they don't unless you do some crazy binning, they don't even all drift the same direction) and the sensors were the same distance from the magnet (the sensing bit isn't centered so if you just put one flipped next to the other one of the sensors is going to be significantly further away from the magnet) it would work. As it is you just get a pretty ugly curve that warps into another ugly curve over temperature. Once you start binning sensors you may as well get a thermally compensated one.
## Why is the magnet facing forward?
Turns out there is a sensor magnet arrangement that gives a linear output for linear displacement, it's just not the one any onf the designs I know of use. Also turns out the people making the sensor know about it, after weeks of trial and error someone pointed me to a [application note](https://www.ti.com/lit/an/slya051a/slya051a.pdf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) by ti that literally had a table (page 5) explaining what I was pretty much brute force mapping out by hand (I can't find who sen't it to me but still thank you). 

# Potential future improvements
I am looking into integrating it with a high resolution filament motion sensor as position data source instead of the motion system.

Other than that I have been using it as it is now for over a year and very similar earlier versions even longer than that.

# Special thanks
- **Deuterious** for the nice blog post proving filament with compensation can be practical
- **Whoever sent me the ti pdf** for making magnets make a bit more sense
- **MiracuruZRH** for testing
- **Blargedy** for proof-reading this monstrosity
- **My glorious local filament manufacturer** for creating the reason to make this and providing extreme samples

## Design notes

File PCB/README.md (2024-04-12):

# Sensor PCB
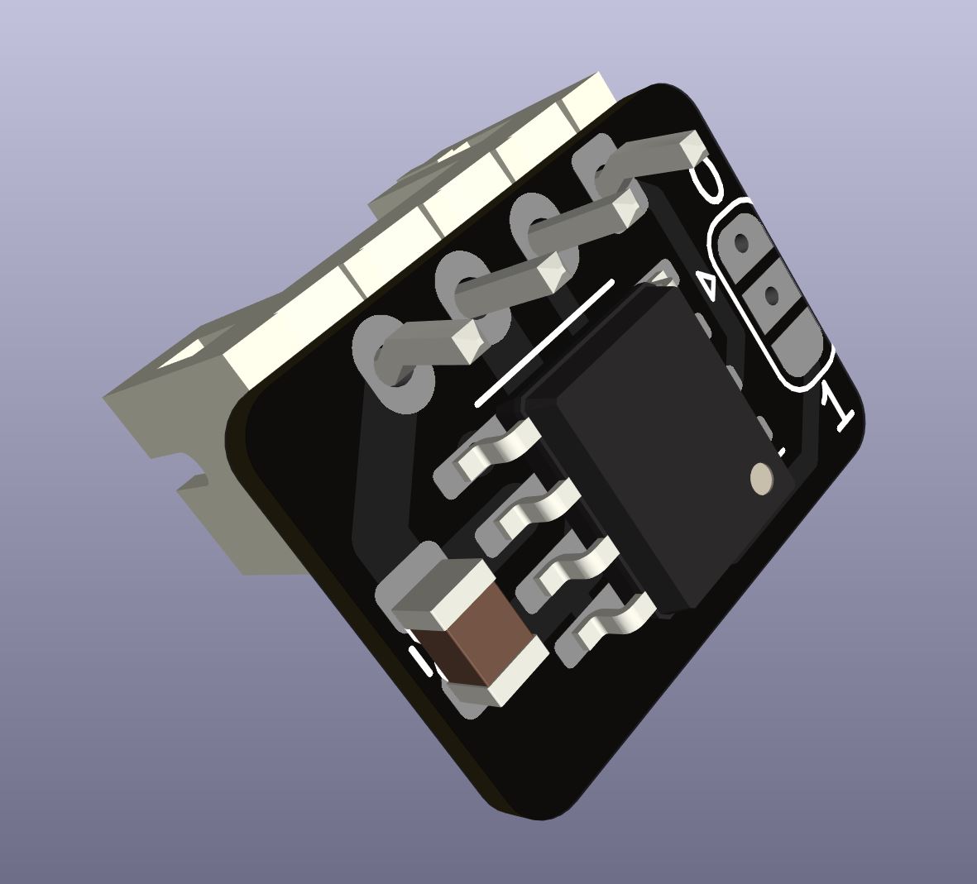
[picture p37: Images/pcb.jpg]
PCB


## BOM
- 1x Sensor PCB
- 1x MLX90395 SOIC8 (Which sub-variant doesn't matter as the settings are set in software)
- 1x 0805 capacitor 22uf (the value is not that important)
- 1x JST PH 4pin through hole male socket

## PCB
ALFws_pcb.zip contains the manufacturing files for the pcb. At the time of writing this both jlcpcb and pcbway produce them quite cheaply.

**The pcb needs to be 0.8mm thick.** No fancy gold plating or anything required.

## Assembly
- Solder on the sensor and it's capacitor.
- Bridge one of the i2c address options (center to 0 or center to 1).
- Solder on the jst ph socket.
- Snip the legs of the jst ph socket to below the height of the sensor

Done.

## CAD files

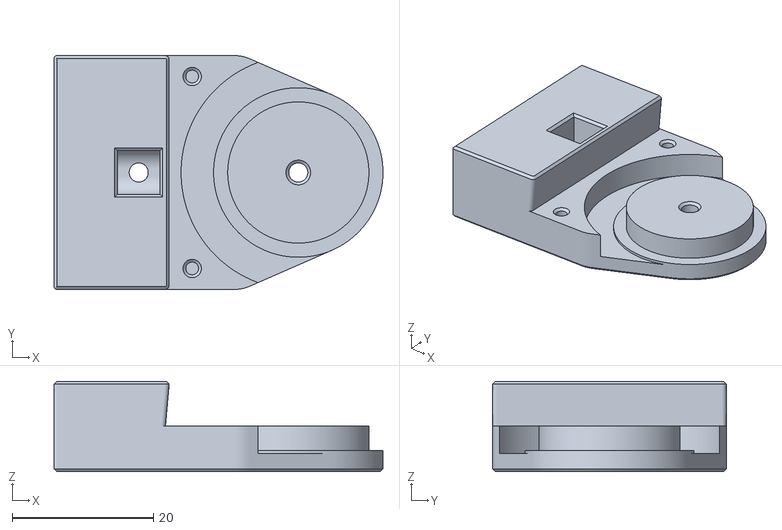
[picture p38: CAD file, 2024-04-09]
STL/MainPlunger.stl
46.6 x 33.1 x 12.8

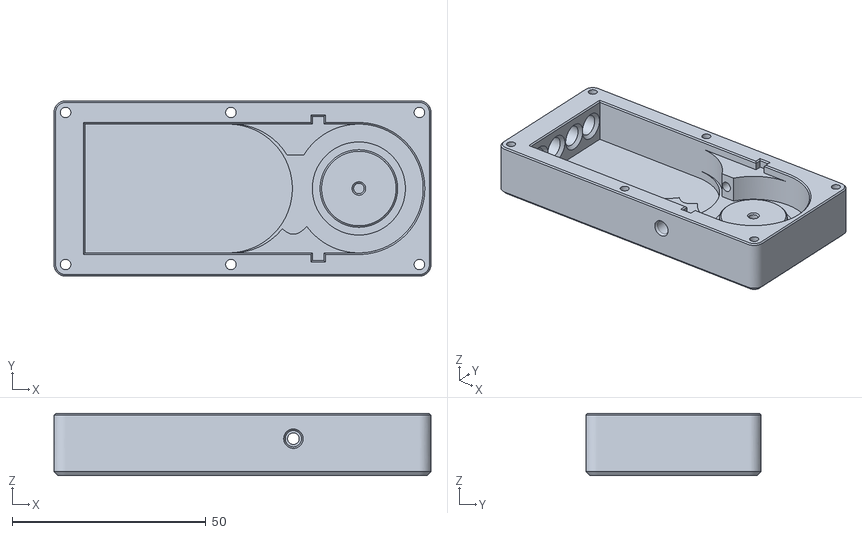
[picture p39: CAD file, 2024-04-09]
STL/MainBody.stl
97.2 x 45.2 x 16.0

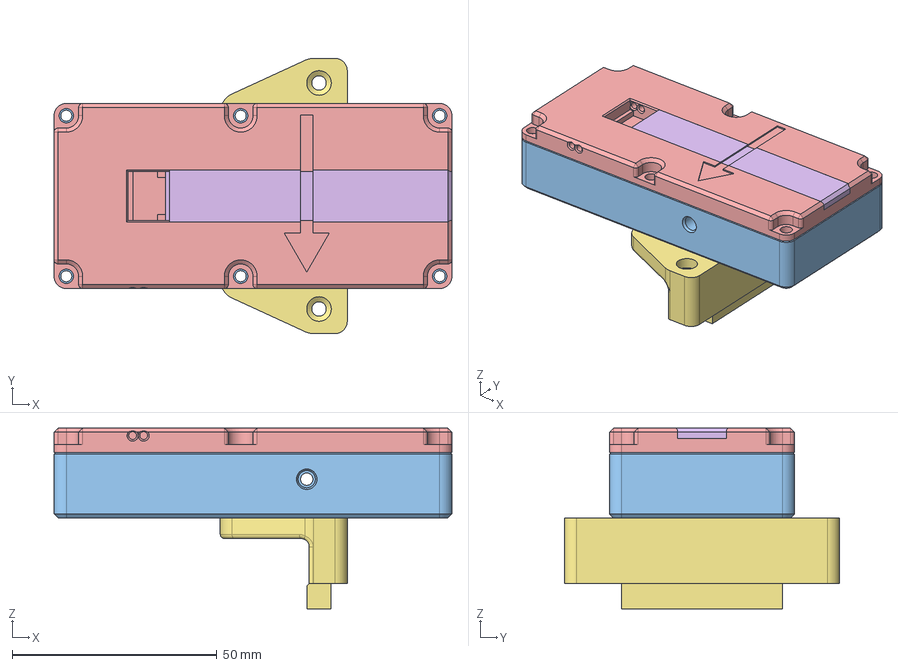
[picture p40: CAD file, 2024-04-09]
CAD/FilamentSensor.step
97.2 x 67.2 x 44.2 mm
Plunger
MainBody
Lid
MountingPlate

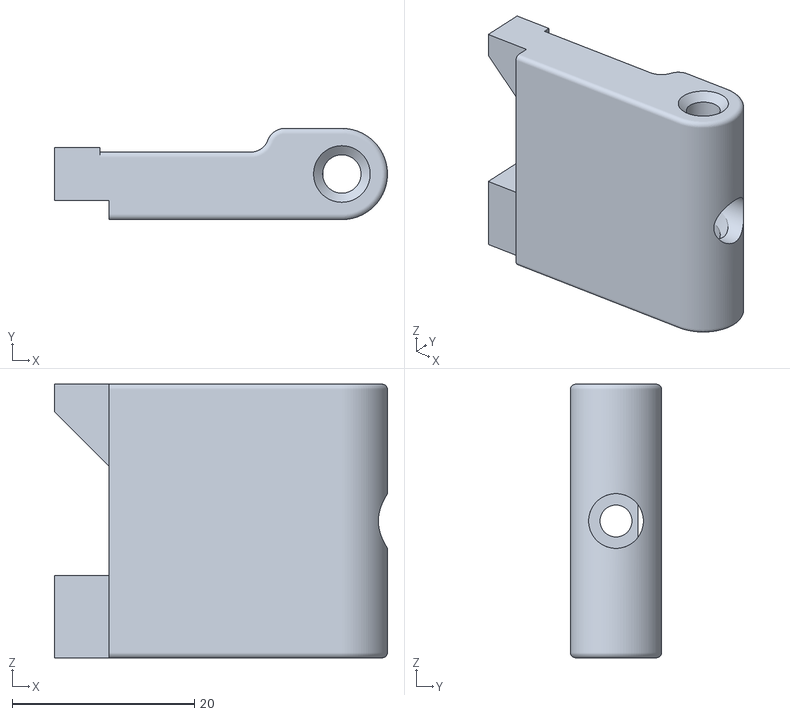
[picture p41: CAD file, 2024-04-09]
STL/Mounting/TubeHolder.stl
36.5 x 10.0 x 30.0

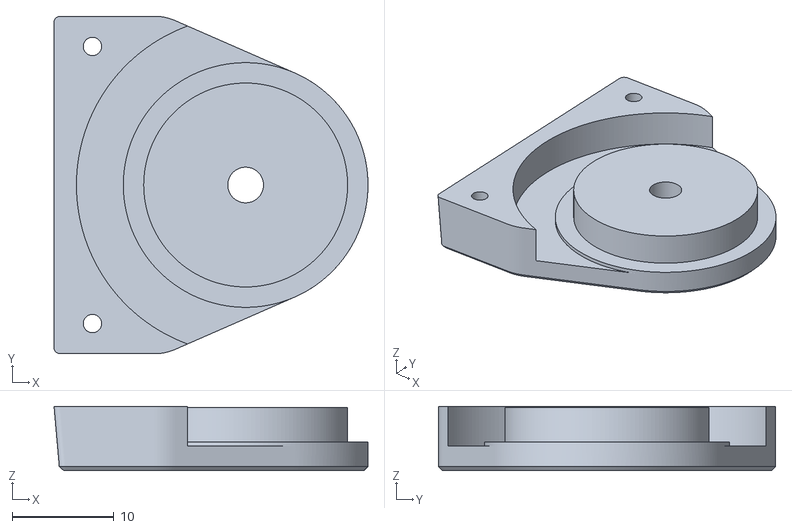
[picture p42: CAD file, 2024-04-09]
STL/BearingTop.stl
30.8 x 33.1 x 6.30

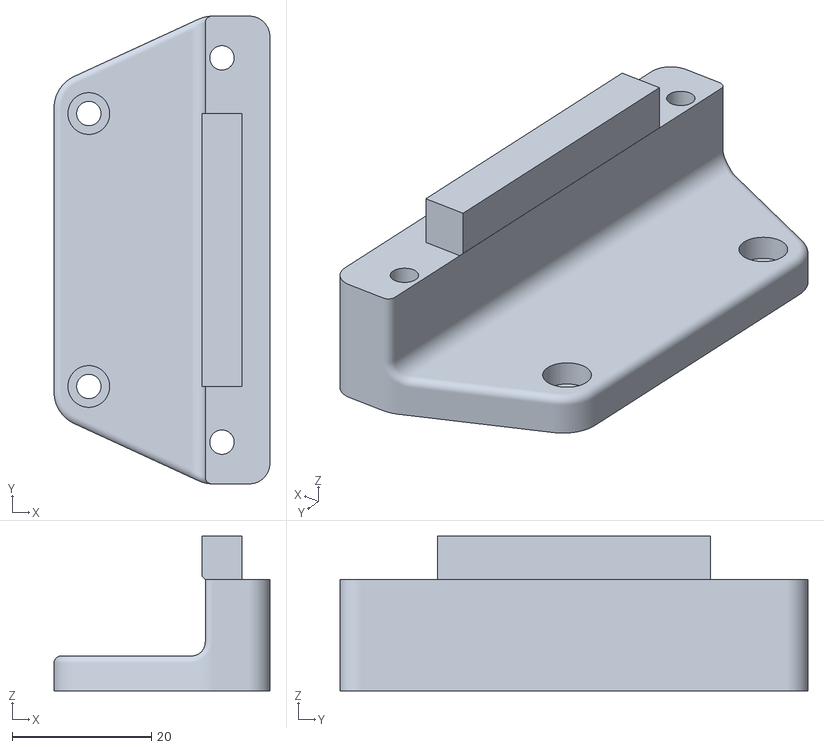
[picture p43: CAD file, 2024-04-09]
STL/Mounting/MountingPlate.stl
31.0 x 67.2 x 22.2

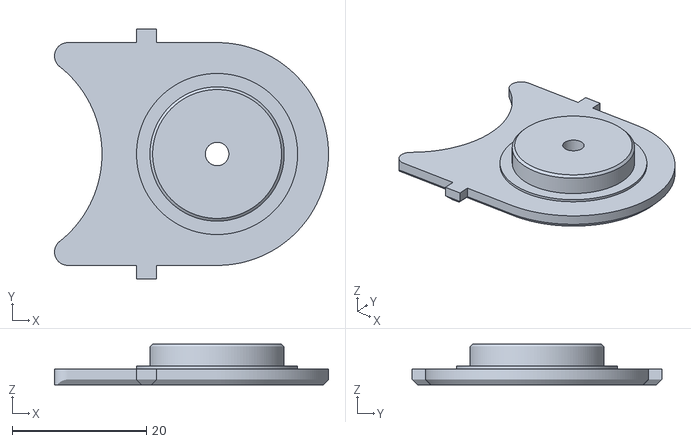
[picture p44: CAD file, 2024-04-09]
STL/BodyBearingHolder.stl
40.8 x 37.2 x 6.10

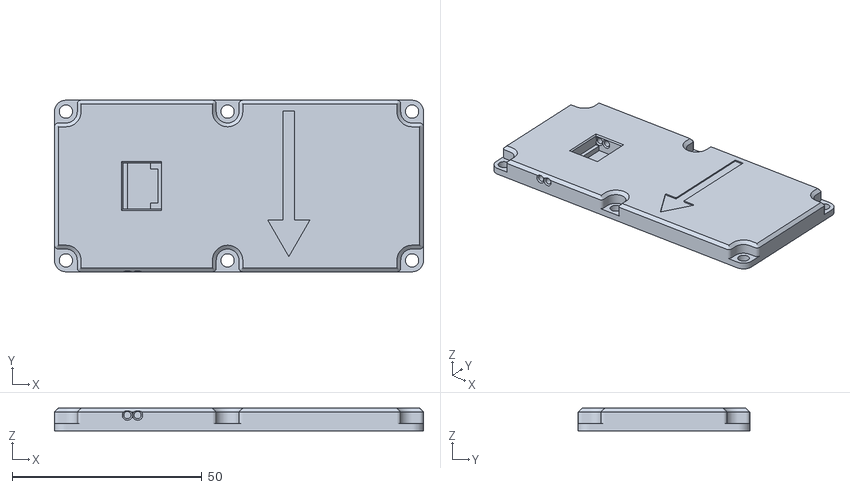
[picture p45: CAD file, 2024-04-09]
STL/Lid.stl
97.2 x 45.2 x 6.00

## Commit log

2024-04-09 initial import
    [BearingTop.stl, BodyBearingHolder.stl, FilamentSensor.step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]
2024-04-12 Update README.md
    Link to the pcb subfolder to reduce confusion
2024-04-12 Update README.md
    Added leg snipping to pcb asembly instructions
